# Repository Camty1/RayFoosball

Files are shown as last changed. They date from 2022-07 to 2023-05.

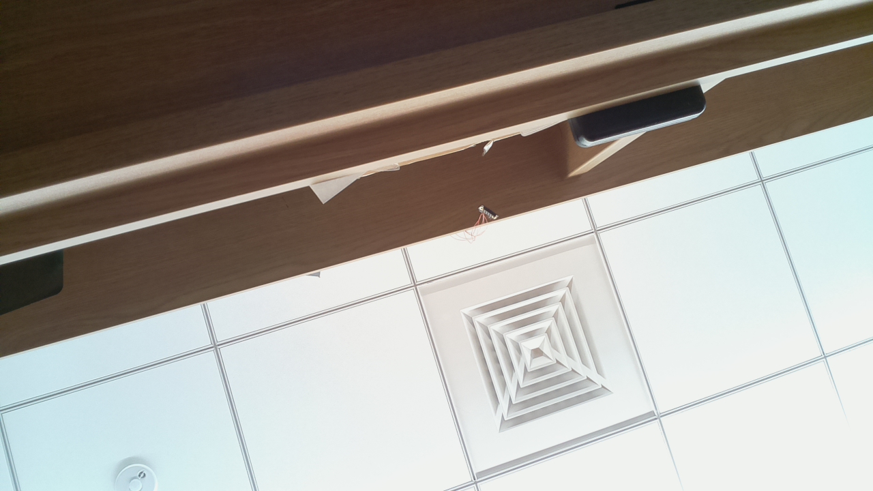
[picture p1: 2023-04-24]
Code/computerVision/images/image0.jpg

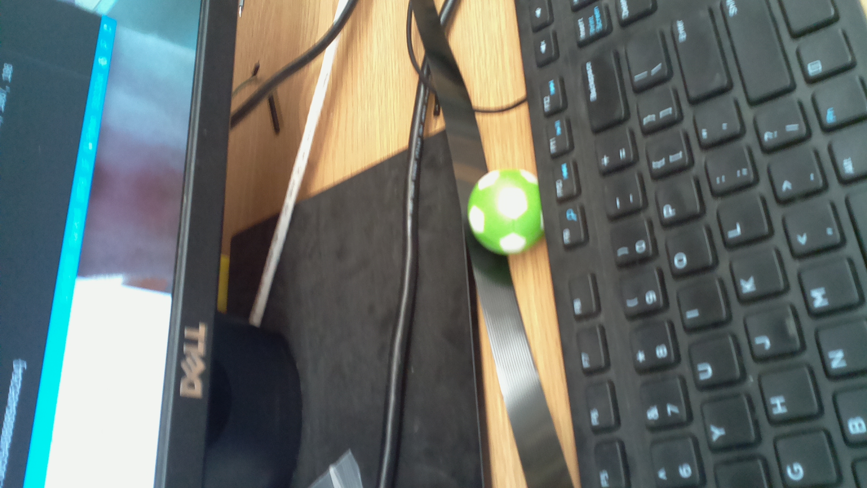
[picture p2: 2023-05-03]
Code/computerVision/images/capture.jpg

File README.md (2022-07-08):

**Ray Robotic Foosball Table**

This is the GITHUB repository for the robotic foosball table in Professor Laura Ray's Lab at the Thayer School of Engineering at Dartmouth College.

The goal of this project is to create a robotic foosball table. Foosball is a tabletop game involving two to four players attempting to hit a ball into each opponent's goal. Each team has four sets of players, goalies, defenders, midfielders, and strikers, connected by a rod that can be moved from side to side or rotated. The simplicity of the players' motion is such that a robot could effectively perform this task using linear and rotational actuators. However, the movement of the players is only one small part of the game. The complexity of foosball arises mainly because the ball moves quickly and unpredictably. The ball can cross the entire length of the table in under a second, and due to the players on the field and the ball's interactions with the walls, it is tough to predict where the ball will go. In addition, there is much strategy involved in the game. Through faking out an opponent, passing between teams, and complex shots like angle shots and bank shots, nearly infinite complexity arises from this theoretically simple game.

This project, which combines sensing, controls, and machine intelligence, is worth pursuing because there are many different avenues of research to explore. For example, to track the ball's movement accurately while leaving enough time to position the players, the system needs to quickly convert visual data into the ball's location while dealing with obstructions caused by the players and people leaning over the table. By taking inspiration from the human brain and tracking only what changes between video frames, machine intelligence researchers significantly reduced the amount of data needed to determine the ball's position (Cohen, 2022). This approach provided a considerable increase in processing speed and is one example of the many possibilities for computer vision research in this project. Outside of image processing, there is considerable potential for applying machine learning (ML) to the system. For example, the system has many low-level actions that it can perform, such as moving the players and hitting the ball. To develop a higher-level strategy, the machine can learn from observing human games or playing against itself in simulation to arrive at an optimal strategy. This is a perfect application for reinforcement learning, genetic algorithms, and other techniques in ML. Finally, since this is a physical system with high demands for speed and precision, there will be a significant emphasis on controls with the potential to use cutting edge techniques in non-linear control and state estimation, optimal control, and adaptive control (Janssen et al., 2012).

This project is not without precedent, with teams from Brigham Young University (BYU) and the École Polytechnique Fédérale de Lausanne (EPFL) creating robotic foosball tables. However, differences in the design and construction of their systems allowed them to focus on different aspects of the game. For example, the team from BYU placed the camera above the table, introducing obstructions and other factors that meant that they had to emphasize computer vision and state estimation (Hollingshead, 2019). The EPFL team, on the other hand, focused on the design of their actuators so that they could move quicker and be more precise (Oberhaus, 2016). From these examples, one can see that this project offers many avenues for exploration.

Outside of research, it can also support multiple different Thayer classes. For example, ENGS 147 Mechatronics is an ideal candidate for the use of this project. This course focuses on the fusion of electronics, mechanical systems, and embedded controls in applications such as robotics. Professor Ray, the instructor of 147, proposed that this system would be an excellent option to explore the software side of robotics and mechatronics and could present an option to explore during the class. Additionally, students in ENGS 108 Applied Machine Learning could use the table to apply techniques developed in the real world. For example, the students could compete to create the best artificial intelligence to control the system. Finally, because people are supposed to play with the project, it has the potential to inspire future engineers. By interacting with the project, children, undergraduates, and adults will see the potential of engineering to tackle interesting problems and its application to many different domains.

Thank you to Professor Laura Ray for her mentorship with the project.  Additionally, thank you to the Mazilu Family for assisting with funding.  This project would not be possible without their help!

*References*

Cohen, G. (2022). Gooaall!!!: Why we built a neuromorphic robot to play Foosball. IEEE Spectrum, 59(3), 44–50. https://doi.org/10.1109/mspec.2022.9729948

Hollingshead, T. (2019, August 12). BYU-created a.i.-powered foosball table goes head to head with humans. BYU News. Retrieved April 11, 2022, from https://news.byu.edu/news/byu-created-ai-powered-foosball-table-goes-head-head-humans

Janssen, R., Verrijt, M., de Best, J., & van de Molengraft, R. (2012). Ball localization and tracking in a highly dynamic table soccer environment. Mechatronics, 22(4), 503–514. https://doi.org/10.1016/j.mechatronics.2012.02.009 

Oberhaus, D. (2016, August 20). This robot will kick your ass at Foosball. VICE. Retrieved April 11, 2022, from https://www.vice.com/en/article/yp355k/foosball-robot

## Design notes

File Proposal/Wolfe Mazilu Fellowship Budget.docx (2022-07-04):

Wolfe Mazilu Engineering Research Fellowship Budget
Item | Cost | Quantity | Total
Foosball Table | 200 | 1 | 200
Raspberry Pi | 75 | 2 | 150
Teensy 4.1 | 30 | 2 | 60
Pi Camera | 30 | 2 | 60
Motor | 100 | 10 | 1000
O Drive | 209 | 5 | 1045
Encoders | 40 | 10 | 400
Ball Screw | 100 | 4 | 400
Pulleys | 50 | 9 | 450
Belts | 10 | 5 | 50
Power Supply | 1000 | 1 | 1000
Off term stipend | 4500 | 1 | 4500
| | Total Cost | 9315

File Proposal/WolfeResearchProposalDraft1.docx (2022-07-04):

Investigations of Learning Algorithms for Robotic Foosball

For the Mazilu Engineering Research Fellowship, I am proposing the creation of a robotic foosball table. Foosball is a tabletop game involving two to four players attempting to hit a ball into each opponent's goal. Each team has four sets of players, goalies, defenders, midfielders, and strikers, connected by a rod that can be moved from side to side or rotated. Because of the relative simplicity of the players' motion, a robot can effectively perform this task using linear and rotational actuators. However, the movement of the players is only one small part of the game. The complexity of foosball arises mainly because the ball moves quickly and unpredictably. The ball can cross the entire length of the table in under a second, but because of the players on the field and the ball's interactions with the walls, it is tough to predict where the ball will be. In addition, there is much strategy involved in the game. Through faking out an opponent, passing between teams, and complex shots like angle shots and bank shots, nearly infinite complexity arises from this theoretically simple game.

This project, which combines sensing, controls, and machine intelligence, is worth pursuing because there are many different avenues of research to explore. For example, to track the ball's movement accurately and have enough time to position the players, the system needs to quickly convert visual data into the ball's location while dealing with obstructions caused by the players and people leaning over the table. By taking inspiration from the human brain and tracking changes in the board, machine intelligence researchers significantly reduced the amount of data needed to determine the ball's position (Cohen, 2022). This approach provided a considerable increase in processing speed and is one example of the many possibilities for computer vision research possible with this project. Outside of image processing, there is significant potential for applying machine learning (ML) to the system. For example, the system has many low-level actions that it can perform, such as moving the players and hitting the ball. To develop a higher-level strategy, the machine can learn from observing human games or playing against itself in simulation to arrive at an optimal strategy. This is a perfect application for reinforcement learning, genetic algorithms, and other techniques in machine learning. Finally, since this is a physical system with high demands for speed and precision, there will be a significant emphasis on controls with the potential to use cutting edge techniques in non-linear control and state estimation, optimal control, and adaptive control (Janssen et al., 2012).

This project is not without precedent, with teams from Brigham Young University and the École Polytechnique Fédérale de Lausanne creating robotic foosball tables. However, differences in the design and construction of their systems allowed them to focus on different aspects of the game. For example, the team from BYU placed the camera above the table, which introduced obstructions and other factors that meant that they had to emphasize computer vision and state estimation (Hollingshead, 2019). The EPFL team, on the other hand, focused on the design of their actuators so that the system could move quicker and be more precise (Oberhaus, 2016). From these examples, one can see that this project offers many avenues for exploration.

Outside of research, it can also support multiple different Thayer classes. For example, ENGS 147 Mechatronics is an ideal candidate for the use of this project. The class focuses on the fusion of electronics, mechanical systems, and embedded controls in applications such as robotics. Professor Ray, the teacher of that class, proposed that this system would be an excellent option to explore the software side of robotics and mechatronics and could present an option to explore during the class. Additionally, students in ENGS 108 Applied Machine Learning could use the table to apply techniques developed in class to a physical system. For example, the students could compete against each other to create the best artificial intelligence to control the system. Finally, because people are supposed to play with the project, it has the potential to inspire future engineers. By interacting with the project, children, undergraduates, and adults will see the potential of engineering to solve complicated problems and its application to many different domains.

Work on the project will start with the creation of the physical hardware. This involves designing the mechanisms for actuation, supports for the camera, and any other necessary changes to the table and will be finished by the end of this spring to culminate my Presidential Scholars research. Then, the project's focus will shift to electronics, combining the vision and actuation systems so that one piece of hardware can control the entire system. This will begin during the spring and extend into the early part of the summer. Finally, the rest of the project will focus on software for the system. This will involve designing controllers for the motors, image processing, trajectory prediction, and strategy development. Additionally, this will involve the development of machine intelligence that will integrate all these tasks into one system. This will make up most of the project and will be the focus of my senior honors thesis, which I will present next spring. This project's advisor, Professor Laura Ray, will help by providing years of expertise in designing and implementing robotic systems. There will inevitably be issues or questions that she will be able to answer. Additionally, she will share potential areas to investigate further as she is up to date with new research occurring in the field.

Finally, I would like to thank Saguaro Technology and Jamie Mazilu Brown for establishing this research fellowship. This fellowship presents the opportunity to dive deep into an engineering research project. The skills I will develop during this project, from research and investigation of literature to hardware and software design, will be crucial in pursuing graduate school and a career in engineering research.

References

Cohen, G. (2022). Gooaall!!!: Why we built a neuromorphic robot to play Foosball. IEEE Spectrum, 59(3), 44–50. https://doi.org/10.1109/mspec.2022.9729948

Hollingshead, T. (2019, August 12). BYU-created a.i.-powered foosball table goes head to head with humans. BYU News. Retrieved April 11, 2022, from https://news.byu.edu/news/byu-created-ai-powered-foosball-table-goes-head-head-humans

Janssen, R., Verrijt, M., de Best, J., & van de Molengraft, R. (2012). Ball localization and tracking in a highly dynamic table soccer environment. Mechatronics, 22(4), 503–514. https://doi.org/10.1016/j.mechatronics.2012.02.009

Oberhaus, D. (2016, August 20). This robot will kick your ass at Foosball. VICE. Retrieved April 11, 2022, from https://www.vice.com/en/article/yp355k/foosball-robot

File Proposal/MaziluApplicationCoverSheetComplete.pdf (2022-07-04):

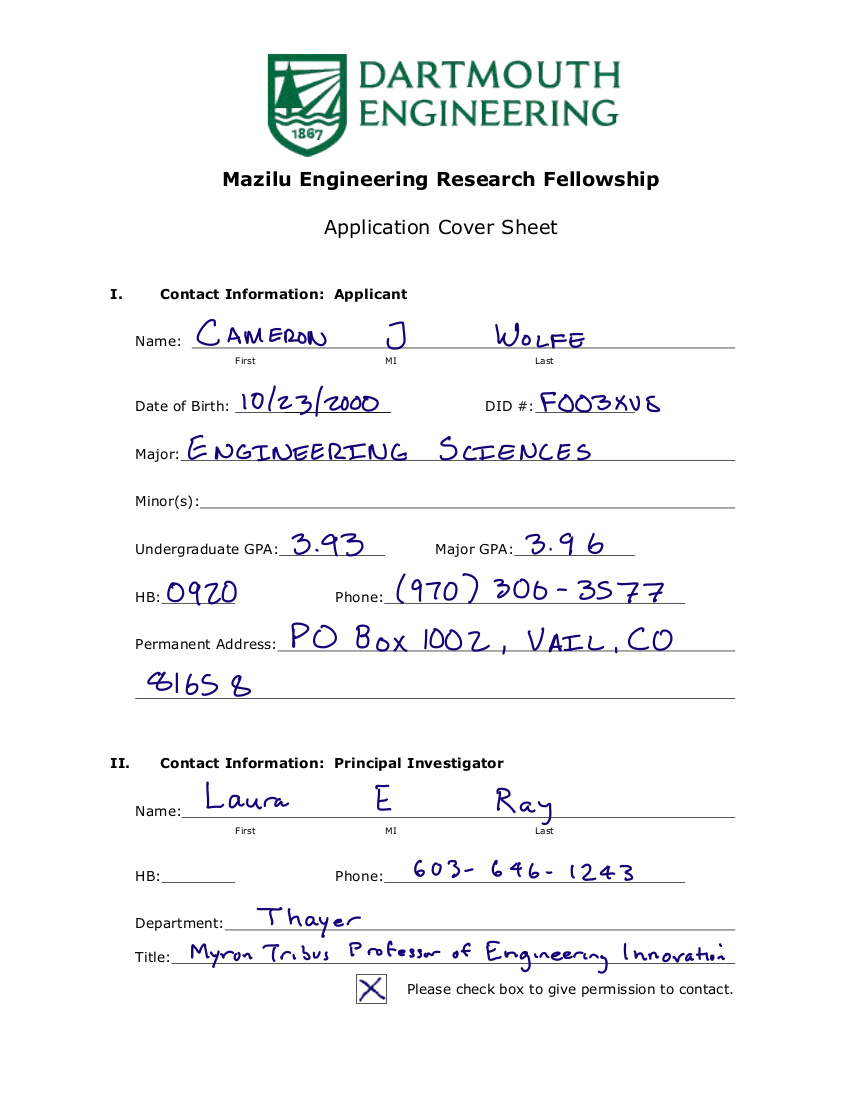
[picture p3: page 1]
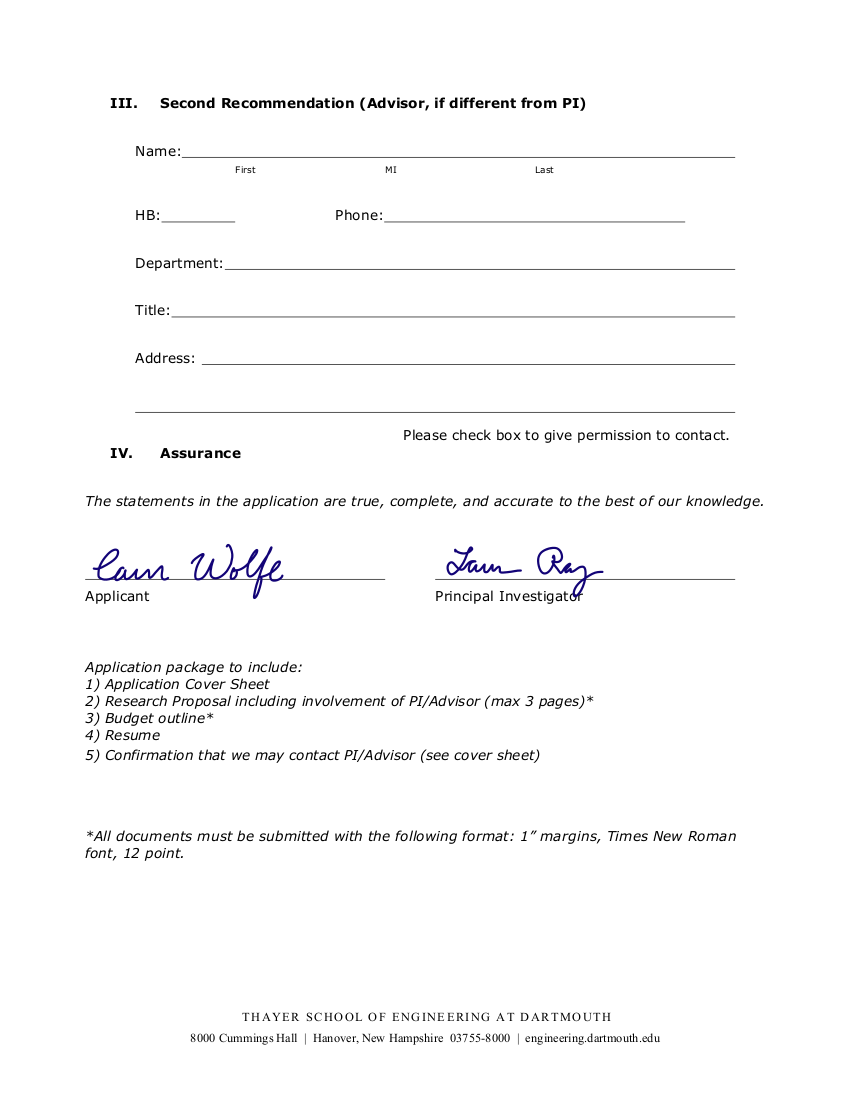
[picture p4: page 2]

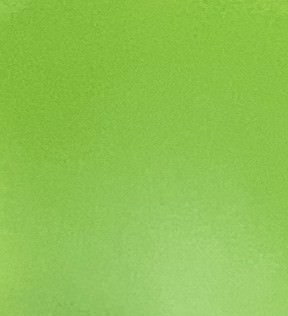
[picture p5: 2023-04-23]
Code/balltest.jpg

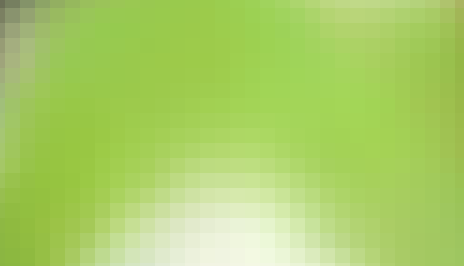
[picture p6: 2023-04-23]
Code/ball2.png

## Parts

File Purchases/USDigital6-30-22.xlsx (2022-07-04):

Part Number | Qty | Price | Description | Product URL | Company | US Digital
E4T-250-250-S-D-D-B | 4 | $26.92 | Ball screw encoder (250 CPR) | https://www.usdigital.com/products/encoders/incremental/kit/e4t | Address | 1400 NE 136th Ave, Vancouver, WA 98684
E4T-720-250-S-D-D-B | 4 | $31.77 | Angular encoder (720 CPR) | https://www.usdigital.com/products/encoders/incremental/kit/e4t | URL | usdigital.com
CA-MIC4-W4-NC-3 | 8 | $8.64 | Encoder wire connector | https://www.usdigital.com/products/accessories/cables/4-pin/ca-mic4-w4-nc/ | Date | 2022-06-30
 |  |  |  |  | Total | $303.88

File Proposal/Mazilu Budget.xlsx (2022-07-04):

Mazilu Budget
Item | Cost | Quantity | Total | Link
Foosball Table | 200 | 1 | 200
Raspberry Pi | 75 | 2 | 150 | https://www.pishop.us/product/raspberry-pi-4-model-b-8gb/?src=raspberrypi
Teensy 4.1 | 30 | 2 | 60 | https://www.pjrc.com/store/teensy41.html
Pi Camera | 30 | 2 | 60 | https://www.pishop.us/product/raspberry-pi-camera-module-v2/?src=raspberrypi
Motor | 100 | 10 | 1000 | https://odriverobotics.com/shop/odrive-custom-motor-d5065
O Drive | 209 | 5 | 1045 | https://odriverobotics.com/shop/odrive-v36
Encoders | 40 | 10 | 400 | https://odriverobotics.com/shop/cui-amt212b
Ball Screw | 100 | 4 | 400 | https://www.amazon.com/Linear-Motion-Ball-Screws/b?ie=UTF8&node=350657011
Pulleys | 50 | 9 | 450 | https://www.mcmaster.com/pulleys/
Belts | 10 | 5 | 50 | https://www.mcmaster.com/drive-belts/xl-series-timing-belts-8/
Power Supply | 1000 | 1 | 1000 | https://www.mouser.com/ProductDetail/MEAN-WELL/BIC-2200-24?qs=aP1CjGhiNiHiKUPZ4cfoIw%3D%3D
Off term stipend | 4500 | 1 | 4500
 |  | Total Cost | 9315

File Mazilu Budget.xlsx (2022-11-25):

Name | Cost | Date | Details | Budget Remaining
Robogaia | $205.33 | 2022-07-01 | Encoder Boards | $747.70
US Digital | $285.07 | 2022-07-05 | Encoders
Stipend | $4500.00 | N/A
THK | $252.94 | 2022-07-06 | Linear Guide Test (Goalie)
Misumi | $512.91 | 2022-07-06 | Ball Screw Test (Goalie)
McMaster | $223.69 | 2022-07-06 | Misc Components Test (Goalie)
McMaster | $58.98 | 2022-08-01 | Aluminum Sheet
Misumi | $1622.46 | 2022-08-05 | Remaining Ball Screws
THK | $805.32 | 2022-08-05 | Remaining Linear Guides
McMaster | $668.40 | 2022-08-05 | Remaining Linear Components
McMaster | $20.02 | 2022-08-12 | #3-48 Screws and Nuts
PJRC | $97.18 | 2022-08-12 | Teensy 4.1s

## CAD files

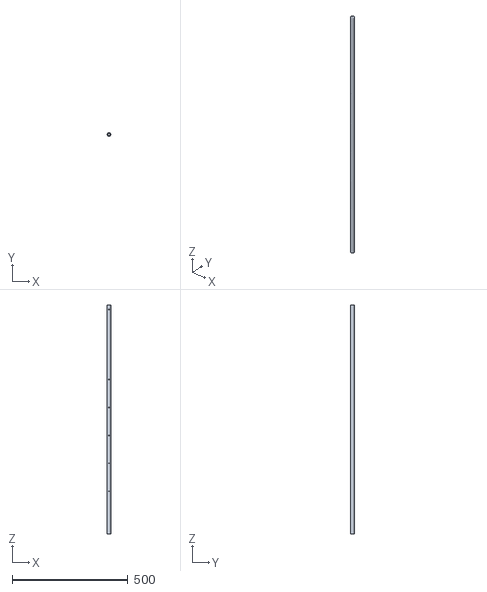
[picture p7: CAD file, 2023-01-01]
Code/simulation/MidfieldRod.obj
15.7 x 15.7 x 987.4

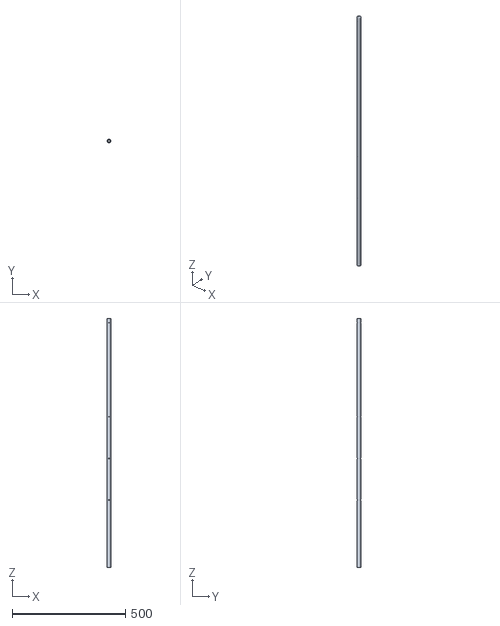
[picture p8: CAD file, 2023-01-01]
Code/simulation/StrikerRod.obj
15.7 x 15.7 x 1101.7

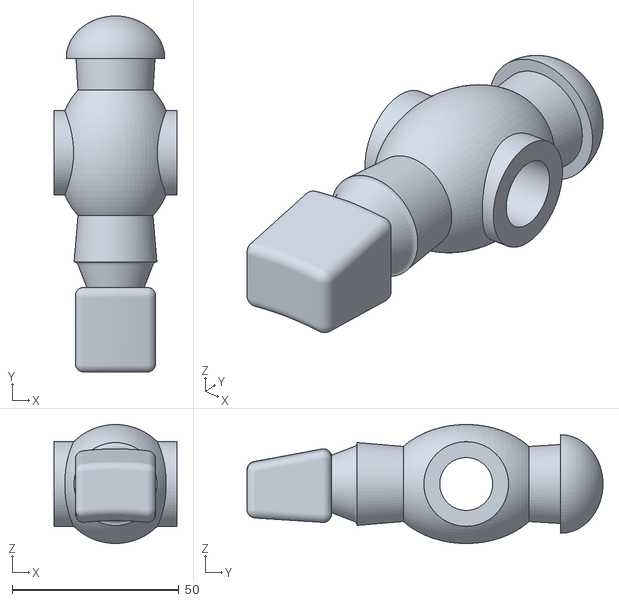
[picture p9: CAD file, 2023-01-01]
Code/simulation/PlayerVisual.obj
36.8 x 106.9 x 35.7

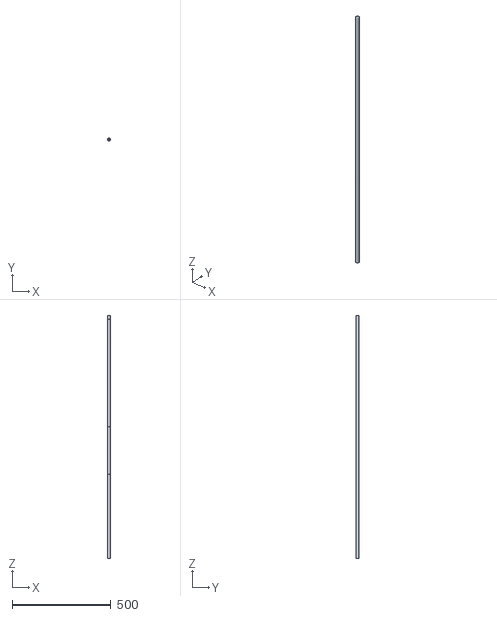
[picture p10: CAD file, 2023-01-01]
Code/simulation/DefenseRod.obj
15.7 x 15.7 x 1228.7

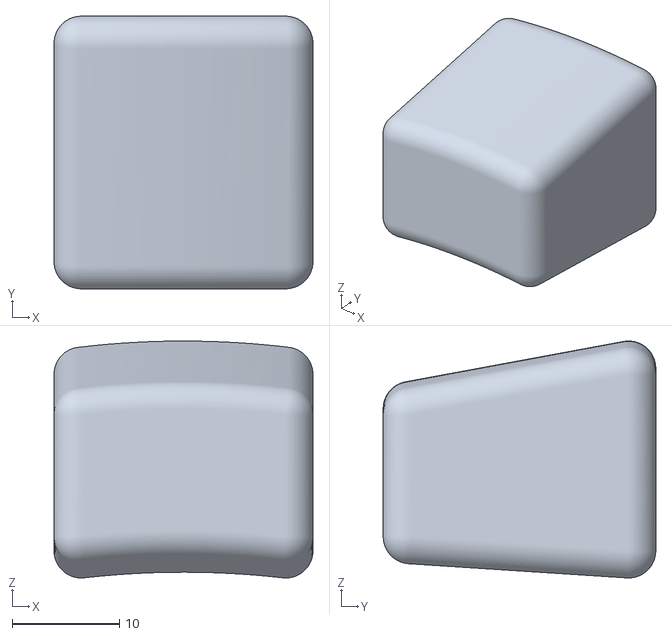
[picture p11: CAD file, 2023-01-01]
Code/simulation/PlayerCollider.obj
24.1 x 25.4 x 22.1

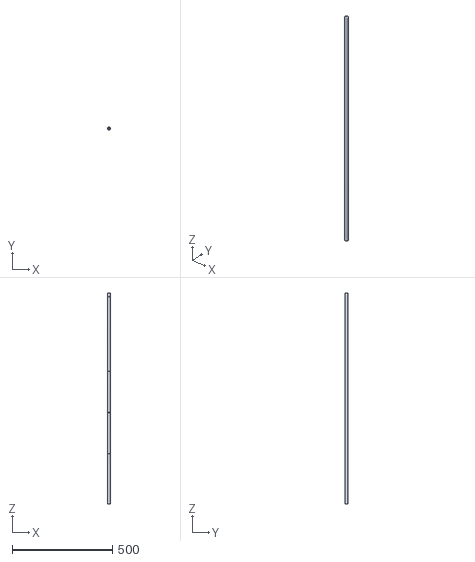
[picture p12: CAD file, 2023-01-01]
Code/simulation/GoalieRod.obj
15.7 x 15.7 x 1054.1

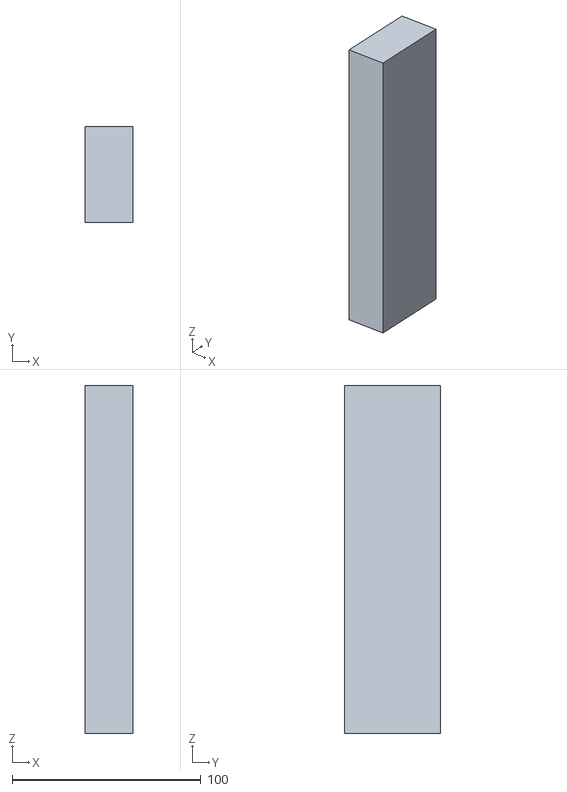
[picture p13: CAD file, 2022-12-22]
Code/simulation/Goal.obj
25.4 x 50.8 x 184.2

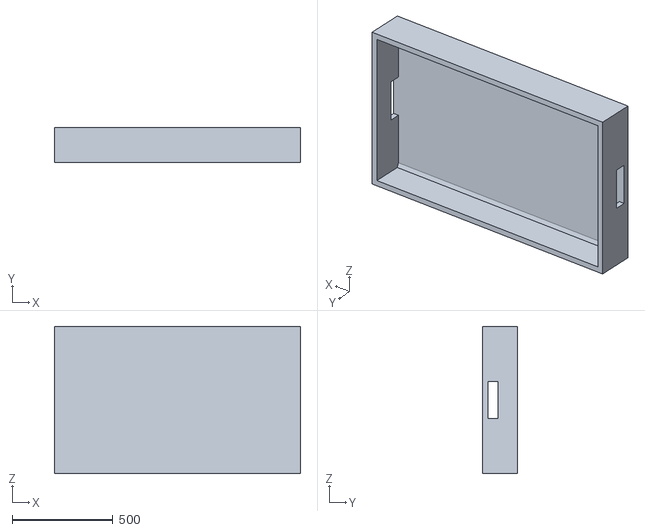
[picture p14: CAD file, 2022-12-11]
Code/simulation/CollisionTable.STL
1219.2 x 171.5 x 730.2

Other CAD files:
Code/simulation/CollisionTable.obj

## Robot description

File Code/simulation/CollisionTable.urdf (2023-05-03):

<?xml version="1.0" ?>
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
<robot name="collision_table">
  <link concave="yes" name="baseLink">
    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
    <inertial>
      <mass value="0"/>
      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
      <origin rpy="1.5707963267948966 0 0" xyz="-.6096 .365125 0"/>
    </inertial>
  </link>
  <link name="goalieBlock1">
    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
    <inertial>
      <mass value="1"/>
      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
      <origin rpy="-1.5707963267948966 0 0" xyz="0 0 0"/>
    </inertial>
  </link>
  <link name="goalieBlock2">
    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
    <inertial>
      <mass value="1"/>
      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
      <origin rpy="-1.5707963267948966 0 0" xyz="0 0 0"/>
    </inertial>
  </link>
  <link name="defenseBlock1">
    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
    <inertial>
      <mass value="1"/>
      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
      <origin rpy="-1.5707963267948966 0 0" xyz="0 0 0"/>
    </inertial>
  </link>
  <link name="defenseBlock2">
    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
    <inertial>
      <mass value="1"/>
      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
      <origin rpy="-1.5707963267948966 0 0" xyz="0 0 0"/>
    </inertial>
  </link>
  <link name="midfieldBlock1">
    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
    <inertial>
      <mass value="1"/>
      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
      <origin rpy="-1.5707963267948966 0 0" xyz="0 0 0"/>
    </inertial>
  </link>
  <link name="midfieldBlock2">
    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
    <inertial>
      <mass value="1"/>
      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
      <origin rpy="-1.5707963267948966 0 0" xyz="0 0 0"/>
    </inertial>
  </link>
  <link name="strikerBlock1">
    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
    <inertial>
      <mass value="1"/>
      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
      <origin rpy="-1.5707963267948966 0 0" xyz="0 0 0"/>
    </inertial>
  </link>
  <link name="strikerBlock2">
    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
    <inertial>
      <mass value="1"/>
      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
      <origin rpy="-1.5707963267948966 0 0" xyz="0 0 0"/>
    </inertial>
  </link>
  <link name="goalieRod1">
    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
    <inertial>
      <mass value="1"/>
      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
      <origin rpy="-1.5707963267948966 0 0" xyz="0 .52075 0"/>
    </inertial>
  </link>
  <link name="goalieRod2">
    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
    <inertial>
      <mass value="1"/>
      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
      <origin rpy="-1.5707963267948966 0 0" xyz="0 0.52705 0"/>
    </inertial>
  </link>
  <link name="defenseRod1">
    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
    <inertial>
      <mass value="1"/>
      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
      <origin rpy="-1.5707963267948966 0 0" xyz="0 0.6143625 0"/>
    </inertial>
  </link>
  <link name="defenseRod2">
    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
    <inertial>
      <mass value="1"/>
      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
      <origin rpy="-1.5707963267948966 0 0" xyz="0 0.6143625 0"/>
    </inertial>
  </link>
  <link name="midfieldRod1">
    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
    <inertial>
      <mass value="1"/>
      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
      <origin rpy="-1.5707963267948966 0 0" xyz="0 0.4937125 0"/>
    </inertial>
  </link>
  <link name="midfieldRod2">
    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
    <inertial>
      <mass value="1"/>
      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
      <origin rpy="-1.5707963267948966 0 0" xyz="0 0.4937125 0"/>
    </inertial>
  </link>
  <link name="strikerRod1">
    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
    <inertial>
      <mass value="1"/>
      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
      <origin rpy="-1.5707963267948966 0 0" xyz="0 0.5508625 0"/>
    </inertial>
  </link>
  <link name="strikerRod2">
    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
    <inertial>
      <mass value="1"/>
      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
      <origin rpy="-1.5707963267948966 0 0" xyz="0 0.5508625 0"/>
    </inertial>
  </link>
  <link name="goaliePlayer11">
    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
    <inertial>
      <mass value="1"/>
      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
      <origin rpy="-1.5707963267948966 0 0" xyz="0 0 0"/>
    </inertial>
  </link>
  <link name="goaliePlayer12">
    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
    <inertial>
      <mass value="1"/>
      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
      <origin rpy="-1.5707963267948966 0 0" xyz="0 0 0"/>
    </inertial>
  </link>
  <link name="goaliePlayer13">
    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
    <inertial>
      <mass value="1"/>
      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
      <origin rpy="-1.5707963267948966 0 0" xyz="0 0 0"/>
    </inertial>
  </link>
  <link name="goaliePlayer21">
    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
    <inertial>
      <mass value="1"/>
      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
      <origin rpy="-1.5707963267948966 0 0" xyz="0 0 0"/>
    </inertial>
  </link>
  <link name="goaliePlayer22">
    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
    <inertial>
      <mass value="1"/>
      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
      <origin rpy="-1.5707963267948966 0 0" xyz="0 0 0"/>
    </inertial>
  </link>
  <link name="goaliePlayer23">
    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
    <inertial>
      <mass value="1"/>
      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
      <origin rpy="-1.5707963267948966 0 0" xyz="0 0 0"/>
    </inertial>
  </link>
  <link name="defensePlayer11">
    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
    <inertial>
      <mass value="1"/>
      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
      <origin rpy="-1.5707963267948966 0 0" xyz="0 0 0"/>
    </inertial>
  </link>
  <link name="defensePlayer12">
    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
    <inertial>
      <mass value="1"/>
      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
      <origin rpy="-1.5707963267948966 0 0" xyz="0 0 0"/>
    </inertial>
  </link>
  <link name="defensePlayer21">
    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
    <inertial>
      <mass value="1"/>
      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
      <origin rpy="-1.5707963267948966 0 0" xyz="0 0 0"/>
    </inertial>
  </link>
  <link name="defensePlayer22">
    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
    <inertial>
      <mass value="1"/>
      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
      <origin rpy="-1.5707963267948966 0 0" xyz="0 0 0"/>
    </inertial>
  </link>
  <link name="midfieldPlayer11">
    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
    <inertial>
      <mass value="1"/>
      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
      <origin rpy="-1.5707963267948966 0 0" xyz="0 0 0"/>
    </inertial>
  </link>
  <link name="midfieldPlayer12">
    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
    <inertial>
      <mass value="1"/>
      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
      <origin rpy="-1.5707963267948966 0 0" xyz="0 0 0"/>
    </inertial>
  </link>
  <link name="midfieldPlayer13">
    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
    <inertial>
      <mass value="1"/>
      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
      <origin rpy="-1.5707963267948966 0 0" xyz="0 0 0"/>
    </inertial>
  </link>
  <link name="midfieldPlayer14">
    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
    <inertial>
      <mass value="1"/>
      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
      <origin rpy="-1.5707963267948966 0 0" xyz="0 0 0"/>
    </inertial>
  </link>
  <link name="midfieldPlayer15">
    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
    <inertial>
      <mass value="1"/>
      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
      <origin rpy="-1.5707963267948966 0 0" xyz="0 0 0"/>
    </inertial>
  </link>
  <link name="midfieldPlayer21">
    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
    <inertial>
      <mass value="1"/>
      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
      <origin rpy="-1.5707963267948966 0 0" xyz="0 0 0"/>
    </inertial>
  </link>
  <link name="midfieldPlayer22">
    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
    <inertial>
      <mass value="1"/>
      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
      <origin rpy="-1.5707963267948966 0 0" xyz="0 0 0"/>
    </inertial>
  </link>
  <link name="midfieldPlayer23">
    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
    <inertial>
      <mass value="1"/>
      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
      <origin rpy="-1.5707963267948966 0 0" xyz="0 0 0"/>
    </inertial>
  </link>
  <link name="midfieldPlayer24">
    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
    <inertial>
      <mass value="1"/>
      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
      <origin rpy="-1.5707963267948966 0 0" xyz="0 0 0"/>
    </inertial>
  </link>
  <link name="midfieldPlayer25">
    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
    <inertial>
      <mass value="1"/>
      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
      <origin rpy="-1.5707963267948966 0 0" xyz="0 0 0"/>
    </inertial>
  </link>
  <link name="strikerPlayer11">
    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
    <inertial>
      <mass value="1"/>
      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
      <origin rpy="-1.5707963267948966 0 0" xyz="0 0 0"/>
    </inertial>
  </link>
  <link name="strikerPlayer12">
    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
    <inertial>
      <mass value="1"/>
      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
      <origin rpy="-1.5707963267948966 0 0" xyz="0 0 0"/>
    </inertial>
  </link>
  <link name="strikerPlayer13">
    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
    <inertial>
      <mass value="1"/>
      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
      <origin rpy="-1.5707963267948966 0 0" xyz="0 0 0"/>
    </inertial>
  </link>
  <link name="strikerPlayer21">
    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
    <inertial>
      <mass value="1"/>
      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
      <origin rpy="-1.5707963267948966 0 0" xyz="0 0 0"/>
    </inertial>
  </link>
  <link name="strikerPlayer22">
    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
    <inertial>
      <mass value="1"/>
      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
      <origin rpy="-1.5707963267948966 0 0" xyz="0 0 0"/>
    </inertial>
  </link>
  <link name="strikerPlayer23">
    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
    <inertial>
      <mass value="1"/>
      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
      <origin rpy="-1.5707963267948966 0 0" xyz="0 0 0"/>
    </inertial>
  </link>
  <joint name="goaliePrismatic1" type="prismatic">
    <origin rpy="0 0 3.14159265" xyz="0.508 0.687705 0"/>
    <parent link="baseLink"/>
    <child link="goalieBlock1"/>
    <limit lower="0" upper=".18161"/>
    <axis xyz="0 1 0"/>
  </joint>
  <joint name="goaliePrismatic2" type="prismatic">
    <origin rpy="0 0 0" xyz="-0.508 -0.687705 0"/>
    <parent link="baseLink"/>
    <child link="goalieBlock2"/>
    <limit lower="0" upper=".18161"/>
    <axis xyz="0 1 0"/>
  </joint>
  <joint name="defensePrismatic1" type="prismatic">
    <origin rpy="0 0 3.14159265" xyz="0.36195 0.859155 0"/>
    <parent link="baseLink"/>
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

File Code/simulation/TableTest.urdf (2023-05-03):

<?xml version="1.0"?>
<robot xmlns:xacro="http://www.ros.org/wiki/xacro" name="collision_table">
    <xacro:property name="rodRadius" value="0.0078613" />
    <xacro:property name="goalieLength" value="1.0541" /> 
    <xacro:property name="defenseLength" value="1.228725" /> 
    <xacro:property name="midfieldLength" value="0.987425" /> 
    <xacro:property name="strikerLength" value="1.101725" />
    <xacro:property name="playerHeight" value="0.0658368" />

    <link concave="yes" name="baseLink">
        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
        <inertial>
            <mass value="0"/>
            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
            <origin rpy="${pi/2} 0 0" xyz="-.6096 .365125 0"/>
        </inertial>
    </link>
    <link name="goalieBlock1">
        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
        <inertial>
            <mass value="1"/>
            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
            <origin rpy="-${pi/2} 0 0" xyz="0 0 0"/>
        </inertial>
    </link>
    <link name="goalieBlock2">
        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
        <inertial>
            <mass value="1"/>
            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
            <origin rpy="-${pi/2} 0 0" xyz="0 0 0"/>
        </inertial>
    </link>
    <link name="defenseBlock1">
        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
        <inertial>
            <mass value="1"/>
            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
            <origin rpy="-${pi/2} 0 0" xyz="0 0 0"/>
        </inertial>
    </link>
    <link name="defenseBlock2">
        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
        <inertial>
            <mass value="1"/>
            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
            <origin rpy="-${pi/2} 0 0" xyz="0 0 0"/>
        </inertial>
    </link>
    <link name="midfieldBlock1">
        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
        <inertial>
            <mass value="1"/>
            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
            <origin rpy="-${pi/2} 0 0" xyz="0 0 0"/>
        </inertial>
    </link>
    <link name="midfieldBlock2">
        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
        <inertial>
            <mass value="1"/>
            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
            <origin rpy="-${pi/2} 0 0" xyz="0 0 0"/>
        </inertial>
    </link>
    <link name="strikerBlock1">
        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
        <inertial>
            <mass value="1"/>
            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
            <origin rpy="-${pi/2} 0 0" xyz="0 0 0"/>
        </inertial>
    </link>
    <link name="strikerBlock2">
        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
        <inertial>
            <mass value="1"/>
            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
            <origin rpy="-${pi/2} 0 0" xyz="0 0 0"/>
        </inertial>
    </link>
    <link name="goalieRod1">
        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
        <inertial>
            <mass value="1"/>
            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
            <origin rpy="-${pi/2} 0 0" xyz="0 .52075 0"/>
        </inertial>
    </link>
    <link name="goalieRod2">
        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
        <inertial>
            <mass value="1"/>
            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
            <origin rpy="-${pi/2} 0 0" xyz="0 ${goalieLength/2} 0"/>
        </inertial>
    </link>
    <link name="defenseRod1">
        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
        <inertial>
            <mass value="1"/>
            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
            <origin rpy="-${pi/2} 0 0" xyz="0 ${defenseLength/2} 0"/>
        </inertial>
    </link>
    <link name="defenseRod2">
        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
        <inertial>
            <mass value="1"/>
            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
            <origin rpy="-${pi/2} 0 0" xyz="0 ${defenseLength/2} 0"/>
        </inertial>
    </link>
    <link name="midfieldRod1">
        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
        <inertial>
            <mass value="1"/>
            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
            <origin rpy="-${pi/2} 0 0" xyz="0 ${midfieldLength/2} 0"/>
        </inertial>
    </link>
    <link name="midfieldRod2">
        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
        <inertial>
            <mass value="1"/>
            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
            <origin rpy="-${pi/2} 0 0" xyz="0 ${midfieldLength/2} 0"/>
        </inertial>
    </link>
    <link name="strikerRod1">
        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
        <inertial>
            <mass value="1"/>
            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
            <origin rpy="-${pi/2} 0 0" xyz="0 ${strikerLength/2} 0"/>
        </inertial>
    </link>
    <link name="strikerRod2">
        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
        <inertial>
            <mass value="1"/>
            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
            <origin rpy="-${pi/2} 0 0" xyz="0 ${strikerLength/2} 0"/>
        </inertial>
    </link>
    <link name="goaliePlayer11">
        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
        <inertial>
            <mass value="1"/>
            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
            <origin rpy="-${pi/2} 0 0" xyz="0 0 0"/>
        </inertial>
    </link>
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

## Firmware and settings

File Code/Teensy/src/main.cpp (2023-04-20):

#include "main.h"



std::default_random_engine randGen;
std::normal_distribution<double> distribution(0.0, 1/3.0);

// Interrupt timer and time step
IntervalTimer timer;
volatile int time = 0;
void stepTime() {
	time++;
	double u = randMotorControl();
	Serial.print(time);
	Serial.print(", ");
	Serial.println(u);
}

// Used to track current state, currently just has time step, but can be used for much more down the road.
// struct State {
// 	int k;
// };



// Given a frequency (rads), a step size, and a current step, outputs the value of a sine function.
double calcSine(double omega, double deltaT, int k) {
	return sin(omega * k * deltaT);
}

// Given a frequency (Hz), a step size, and a current step, outputs the value of a sine function.
double calcSineHz(double f, double deltaT, int k) {
	return sin(2 * M_PI * f * k * deltaT);
}

// Returns a normally distributed input around 0 with sigma = 1/6;
double getRandomInput() {
	return distribution(randGen);
}

// Reads from the USB Serial and outputs the integer given
int readIntInput() {

	// Allocates variable to store bytes
	int incomingByte;

	// Vector to store the digits recieved
	std::vector<int> values(0);

	// Read from Serial
	while (Serial.available()) {
		incomingByte = Serial.read();

		// Send what was recieved back, useful for debugging
    	Serial.print("USB received: ");
    	Serial.println(incomingByte, DEC);
		values.push_back(incomingByte);
	}

	// Remove 'n'
	values.pop_back();

	// Initialize variables for value calculation
	int value = 0;
	int counter = 0;

	// Handle negative inputs
	int negative = values[0] == 45;

	// Calculate value by going through places, starting with the one's place (end of values vector)
	while (!values.empty()) {
		int currentDigit = values.back() - 48;
		// Make sure digit is valid (in range [0,9]) and then add digit  10^place to value.
		value += (currentDigit >= 0 && currentDigit <= 9) ? currentDigit * (int) pow(10.0, (double) counter) : 0;
		values.pop_back();
		counter++;
	}
	return !negative ? value : -value;
}

// Function to control motor based on user input
void inputMotorControl() {

	if (Serial.available()) {
    	int value = readIntInput();
		Serial.print("Calculated value: ");
		Serial.println(value, DEC);
		double norm = value/256;
		MotorCommand cmd = generateCommand(norm);
		driveMotor(cmd, PWMFORWARD, PWMBACKWARD);
  	}
}

// Function to control motor with sine wave input
void sineMotorControl(double omega, int us) {
	// Copying of time step will get messed up if interrrupt occurs at same time, therefore no interrupt is called
	noInterrupts();
	int k = time;
	interrupts();

	// Get time step size from microseconds
	double deltaT = us/1000000.0;
	
	// Calculate sin value
	double value = calcSine(omega, deltaT, k);

	// Drive motor
	MotorCommand cmd = generateCommand(value);
	driveMotor(cmd, PWMFORWARD, PWMBACKWARD);
}

// Function to control motor with random input (useful for SYS-ID)
double randMotorControl() {
	// Get random input for motor
	double rand = getRandomInput();

	// Drive motor
	MotorCommand cmd = generateCommand(rand);
	driveMotor(cmd, PWMFORWARD, PWMBACKWARD);
	return rand;
}

// Called once at startup
void setup() {

	// Digital pins
	pinMode(PWMBACKWARD, OUTPUT);
	pinMode(PWMFORWARD, OUTPUT);
	pinMode(BALL_CS, OUTPUT);
	pinMode(ROT_CS, OUTPUT);

	// SPI setup
	digitalWrite(BALL_CS, HIGH);
	digitalWrite(ROT_CS, HIGH);


	// USB serial
	Serial.begin(9600);

	// Turn off motors at start
	analogWrite(PWMFORWARD, 0);
	analogWrite(PWMBACKWARD, 0);

	// Time step
	// TODO: Attach interrupt to external pin for system clock signal
	timer.begin(stepTime, TS_US);
}

// Called every frame
void loop() {
	//inputMotorControl();
	//sineMotorControl(.5 * M_PI * 2, TS_US);
}

int main(void) {
	setup();
	while (1) {
		loop();
	}
	return -1;
}

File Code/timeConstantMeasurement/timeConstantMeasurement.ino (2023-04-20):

#include <SPI.h>

#define NUM_SAMPLES 10
#define TIME_STEPS 300

IntervalTimer clock100;

double u;
int counter = 0;
int state = 0;
int measurement = 0;
int clkFlag = 0;

int motorCW = 0;
int motorCCW = 1;
int encoderCS = 26;

double motorMagnitudes[NUM_SAMPLES];

void setup() {

    for (int i = 0; i < NUM_SAMPLES; i++) {
        motorMagnitudes[i] = ((double) (i+1))/((double) NUM_SAMPLES);
    }
    
    // Pin setup
    pinMode(encoderCS, OUTPUT);
    digitalWrite(encoderCS, HIGH);
    
    // Communication protocol init
    SPI.begin();
    Serial.begin(115200);

    // Setup encoder chip
    digitalWrite(encoderCS, LOW);
    SPI.transfer(0x88);
    SPI.transfer(0x03);
    digitalWrite(encoderCS, HIGH);

    // Begin interval timer
    clock100.begin(clk, 1000);
}

void loop() {
    driveMotor(u);
    if (measurement == NUM_SAMPLES) {
        state = 6;
    }
    if (clkFlag) {
        switch(state) {
            case 0:
                u = 0.0;
                printState();
                counter ++;
                break;
            case 1:
                u = motorMagnitudes[measurement];
                printState();
                counter ++;
                break;
            case 2: 
                u = 0.0;
                printState();
                counter ++;
                break;
            case 3:
                u = -motorMagnitudes[measurement];
                printState();
                counter ++;
                break;
            case 4:
                u = 0.0;
                printState();
                counter ++;
                break;
            case 5:
                u = 0.0;
                measurement ++;
                state = 1;
                counter = 0;
            default:
                u = 0.0;
                break;
        }
        if (counter >= TIME_STEPS) {
            state ++;
            counter = 0;
        }
        clkFlag = 0;
    }
}

void clk() {
    clkFlag = 1;
}

void driveMotor(double u) {
    
    int magnitude = (int)(fabs(u) * 255);
    
    if (u < 0) {
        analogWrite(motorCW, 0);
        analogWrite(motorCCW, magnitude);
    }
    else if (u > 0) {
        analogWrite(motorCW, magnitude);
        analogWrite(motorCCW, 0);
    }
    else {
        analogWrite(motorCW, 0);
        analogWrite(motorCCW, 0);
    }

}

void printState() {
    unsigned long t = micros();
    long count = getEncoderData(encoderCS);
    Serial.print(t);
    Serial.print(",");
    Serial.print(u, 3);
    Serial.print(",");
    Serial.println(count);
}

long getEncoderData(int CS) {
    long dataOut = 0;
    uint8_t dataByte; 
    // Handle SPI CS
    digitalWrite(CS, LOW);
    
    // Get encoder data
    SPI.transfer(0x60);
    for (int i = 0; i < 4; i++) {
        dataByte = SPI.transfer(0x00);
        dataOut = dataOut << 8;
        dataOut = dataOut | (long)dataByte;
    }
    digitalWrite(CS, HIGH);
    
    return dataOut;
}

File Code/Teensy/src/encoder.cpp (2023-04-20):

#include "encoder.h"

namespace encoder
{
    // Contains tick counts for both ball screw and rotation encoders
    struct EncoderData {
        long ball;
        long rot;

        void zero(EncoderData *zeroPos) {
            this->ball -= zeroPos->ball;
            this->rot -= zeroPos->rot;
        }

    };

    // Contains a linear and angular position doubles
    // TODO: Determine if quadrature counts are 4 * number of slits or not
    struct PositionData {
        double ball;
        double rot;

        void convert(encoder::EncoderData *encoderData) {
            this->ball = encoderData->ball/250;
            this->rot = encoderData->rot/720;
        }
    }

    void LS7366_Init(void) {
    
        // SPI initialization
        SPI.begin();
        delay(10);
    
        // Configure ball screw encoder
        digitalWrite(BALL_CS,LOW);
        SPI.transfer(0x88); 
        SPI.transfer(0x03);
        digitalWrite(BALL_CS,HIGH);

        // Configure rotation encoder
        digitalWrite(ROT_CS,LOW);
        SPI.transfer(0x88); 
        SPI.transfer(0x03);
        digitalWrite(ROT_CS,HIGH); 
    }

    // Uses SPI to get tick count from encoders and updates EncoderData struct
    void getEncoderData(EncoderData* encoders) {

        // Get data from ball screw encoder
        digitalWrite(BALL_CS, LOW);
        encoders->ball = encoderRead();
        digitalWrite(BALL_CS, HIGH);

        // Get data from rotation encoder
        digitalWrite(ROT_CS, LOW);
        encoders->rot = encoderRead();
        digitalWrite(ROT_CS, HIGH);
        
    }

    // Handles communication with encoder by sending 4 empty bytes.
    // NOTE: CS pin is not handled in this function.
    long encoderRead() {
        // Initialize data
        long data = 0;

        // Read from encoder, combining the 4 bytes of signal into one value.
        for (int i = 0; i < 4; i++) {
            data << 8;
            data += SPI.transfer(0xFF); // Dummy bytes to read from MISO line
        }

        return data;
    }
}

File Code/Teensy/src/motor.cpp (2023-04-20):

#include "motor.h"
namespace motor {

    // MotorCommands contain the PWM value [0, 256] for both the forward and backward reference input.
    // NOTE: Either forward or backward should be non-zero, not both at the same time.
    struct MotorCommand {
	    int fwd;
	    int bwd;
    };

    // Takes a double in the range [-1, 1] and converts it to a MotorCommand. Enforces saturation if command is too big
    MotorCommand generateCommand(double in) {
	    // Initialize cmd and give it stop command.
	    MotorCommand cmd;
	    cmd.fwd = 0;
	    cmd.bwd = 0;

	    // Invalid input
	    if (abs(in) > 1) {
		    in = in/abs(in);
	    }
	
	    // Take input and converts it to MotorCommand, changing whether forward or backward is zero depending on the sign of the input
	    cmd.fwd = (in > 0) ? (int) round(256 * in) : 0;
	    cmd.bwd = (in < 0) ? (int) round(-256 * in) : 0;

	    return cmd;
    }

    // Takes a MotorCommand and PWM pins to drive the motor for the command.
    // NOTE Does not check to see if one of the directions is 0
    void driveMotor(MotorCommand cmd, int forwardPin, int backwardPin) {
    	analogWrite(forwardPin, cmd.fwd);
	    analogWrite(backwardPin, cmd.bwd);
    }
}

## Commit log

2022-07-04 V2 Ball Screw Assembly
    Using Misumi components as opposed to cheap ball screw, replacing amazon encoders with US Digital encoders. Finally created the repo for this
    [1277N735_Corrosion-Resistant Timing Belt Pulley.SLDPRT, 1375K39_MXL Series Timing Belt Pulley.SLDPRT, 2464K22_Clamping Precision Flexible Shaft Coupling.SLDPRT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]
2022-07-04 Removed unused components
    [SHS30C1SS_280L_G20_0_B_M6F_87_0_0_0_1_.sldasm, SHS30C1SS_280L_G20_0_B_M6F_87_0_0_0_1__3.sldprt, SHS30C1SS_280L_G20_0_B_M6F_87_0_0_0_1__5.sldprt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]
2022-07-04 Remove more unused components
    Apparently it didn't work last time or something
    [SHS30V1SS_280L_G20_0_B_M6F_87_0_0_0_1_.sldasm, SHS30V1SS_280L_G20_0_B_M6F_87_0_0_0_1__3.sldprt, SHS30V1SS_280L_G20_0_B_M6F_87_0_0_0_1__5.sldprt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]
2022-07-08 Data Collection
    Found the transfer function for the motor with the chinese ball screw
    [1,5V-07082022.csv, BallScrewLengthCalcs.xlsx, Mazilu Budget.xlsx]
2022-07-12 More data collection
    Need to find a way to standardize the time steps from video frames
    [07112022-01.csv, 07112022-04.csv, 07112022-09.csv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]
2022-07-15 Manufacturing drawings + snake RL
    made a rod coupler yesterday. Made some updates today and will make 4 of them next week. Also, to get practice with RL, I am creating a snake game and then training it to play.
    [07142022-01-ROD-MOTOR_COUPLER.SLDDRW, Flat pattern - HorizontalMotorMount.DXF, Flat pattern - RotationMotorHolder.DXF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]
2022-07-15 More Work on Snake RL
    Working on getting matlab model to train. Have to create data store which is a little frustrating but oh well
    [MotorRodCoupler.SLDPRT]
2022-07-16 Switching snake to python
    Matlab doesn't give me the flexibility I want with my neural networks, so I am going to try python instead even though I don't like it as much
2022-07-21 Update sheet thickness
    [07142022-01-ROD-MOTOR_COUPLER.SLDDRW, 07212022-01-BALL-MOTOR-HOLDER.SLDDRW, 07212022-01-ROTATION-MOTOR-HOLDER.SLDDRW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]
2022-08-11 Working w/ Teensy
    [BallScrewLengthCalcs.xlsx, Mazilu Budget.xlsx]
2022-08-11 Fixing gitignore
    [07212022-01-BALL-MOTOR-HOLDER.SLDDRW, 07212022-01-ROTATION-MOTOR-HOLDER.SLDDRW, 1375K39_MXL Series Timing Belt Pulley.SLDPRT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]
2022-08-11 Teensy Docker for Ubuntu Going to install Ubuntu on computer so I can write to teensy easier. Won't have to manually load the file onto the teensy.
2022-08-11 Created PWM output logic for motor control Built project using teensy docker module, use teensyduino to flash generated hex file
2022-08-12 Removed teensy_docker as a submodule This was preventing changes to the code (specifically teensy code) being tracked. Should be fixed now
2022-08-12 Added /Code/Teensy/ to tracked files Hold over of the submodule. Should be good now
2022-08-12 Finished sine input and random motor control Now need to work on setting up encoders so they can be added to the software
2022-08-16 Added encoder handling
2022-08-17 Budget update and papers
    [07212022-01-BALL-MOTOR-HOLDER.SLDDRW, 07212022-01-ROTATION-MOTOR-HOLDER.SLDDRW, BallMotorHolder.SLDPRT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]
2022-11-25 IO changes and Tinkering with Simulation
    [soccer_output.csv]
2022-12-11 Created mesh behavior, now need STL files
    [soccer_output.csv]
2022-12-11 Table STL added
    [CollisionTable.STL]
2022-12-22 Table Simulation with main body, ball, and goals. Next is goal detection and adding the players
    [CollisionTable.STL, CollisionTable.obj, CollisionTable.urdf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]
2022-12-26 Change origins of table and goal urdfs
    [CollisionTable.urdf, Goal.urdf]
2023-01-01 Added goalie from white team Not sure about the way I did it. Tried to have a ghost joint so I could include both translation and rotation, but did not work. Instead have rod translate and players ro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
    [CollisionTable.urdf, DefenseRod.obj, GoalieRod.obj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]
2023-04-20 Finally fixed git on laptop. Uploading many tings but PPO and sim is big change
    [PPO_log_full_state_0.csv, PPO_log_full_state_1.csv, PPO_log_full_state_10.csv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]
2023-04-22 added babylon support for single agent training
    [PPO_log_full_state_0.csv, PPO_log_full_state_1.csv, PPO_log_full_state_2.csv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]
2023-04-23 urdf updates, still trying to track down ball speed during striker start
    [CollisionTable.urdf, TableTest.urdf]
2023-04-25 Added babylon arg parser since it cannot use cuda
    [PPO_log_full_state_47.csv]
2023-04-25 This time might do it
    [07142022-01-ROD-MOTOR_COUPLER.SLDDRW, 07212022-01-BALL-MOTOR-HOLDER.SLDDRW, 07212022-01-ROTATION-MOTOR-HOLDER.SLDDRW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]
2023-04-26 running decentralized training on babylon
    [PPO_log_decentralized_full_0.csv, PPO_log_decentralized_full_1.csv, PPO_log_decentralized_full_2.csv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]
2023-05-03 a couple edits to the cv main testing files
2023-05-03 ppo v2 start
    [PPO_log_0.csv, PPO_log_1.csv, PPO_log_10.csv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]
2023-05-04 cant track
2023-05-04 printing a lot
2023-05-06 fixed zer zero length is terminal array bug
    [PPO_log_full_state_0.csv, PPO_log_full_state_1.csv]
2023-05-06 trying training with just goal. Previous training worked a little bit but not really that well tbh
    [PPO_log_full_state_13.csv, PPO_log_full_state_14.csv, PPO_log_full_state_15.csv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]
2023-05-06 tried training with V2, did not work
    [PPO_log_just_team_0.csv, PPO_log_just_team_1.csv, PPO_log_just_team_2.csv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]
2023-05-07 just goal training. Went ver fast with what seemed no reward tracking
    [PPO_log_0.csv, PPO_log_1.csv, PPO_log_10.csv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]
